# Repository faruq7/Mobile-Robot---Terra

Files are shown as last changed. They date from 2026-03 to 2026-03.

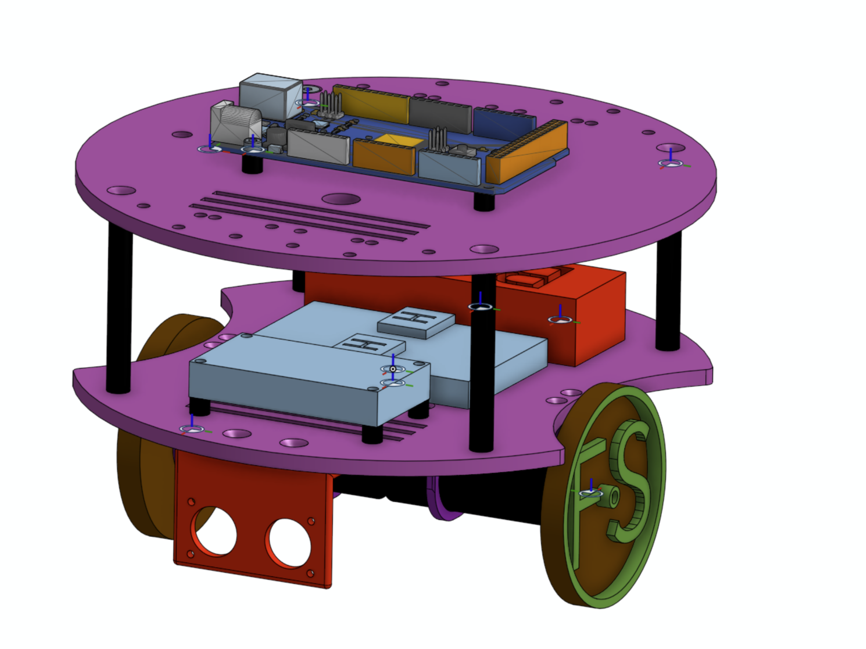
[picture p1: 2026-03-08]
CAD/Assembly/Assembly Image.png

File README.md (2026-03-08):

Objective:
To develop a mobile robot that is capable of reliable motion control, obstacle detection, and basic autonomous manoeuvres.

Mechanical & System Design:
•	Designed and modelled full chassis assembly in CAD using Onshape, including the motors, mounts, and incorporating techniques like clearance and interference checks to ensure ease of production and efficient assembly. 
•	Mechanical components were 3D printed and the electronics researched and then sourced.
•	Integrated dual DC motors with encoders for feedback-based motion control.
•	Utilised ultrasonic sensors for obstacle detection.
•	Developed program using the Arduino IDE.

Motion Control & Behaviour:
The robot was programmed using state machine logic to manage driving states which included:
•	Forward
•	Reverse
•	Left / Right turns
•	Three-point turn manoeuvre

Main Problem Encountered:
The robot had a slight drift to the left when doing standard forward motion. This highlighted there was unequal motor revolutions despite the motors possessing the same gear difference and drive commands.
Solution
The Encoder difference was then logged to an SD card during the forward motion. The data highlighted a substantial difference with the motor revolutions, confirming the imbalance of velocity between motors.
Proportional (P) control was then implemented with the aim of reducing the velocity difference between motors based on the encoder feedback.

Outcome
The forward motion drift had reduced slightly, although small cumulative error remains as on P control was implemented. Integral control will be added to compensate for the accumulated drift over longer distances.
Project Overview
System Architecture
Hardware
Software
How to Run
Images / CAD
Future Improvements

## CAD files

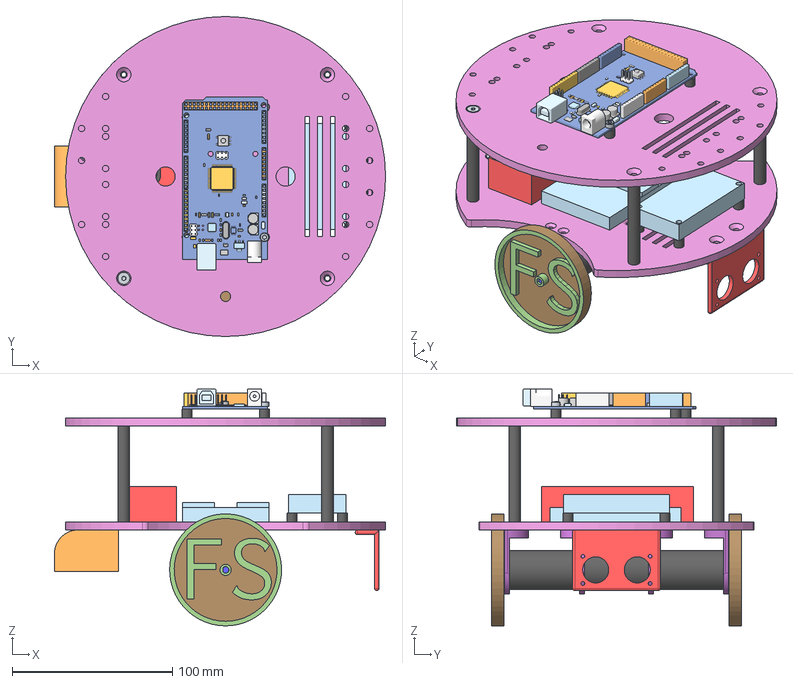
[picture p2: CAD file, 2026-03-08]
CAD/Assembly/Assembly 1.step
207.0 x 200.0 x 148.0 mm
Hex socket countersunk head screw M4x0.7 x 10 x 2
Hex socket countersunk head screw M4x0.7 x 40
Castor Spacer
Hex socket head cap screw M3x0.50 x 12
Hex socket countersunk head screw M4x0.7 x 35

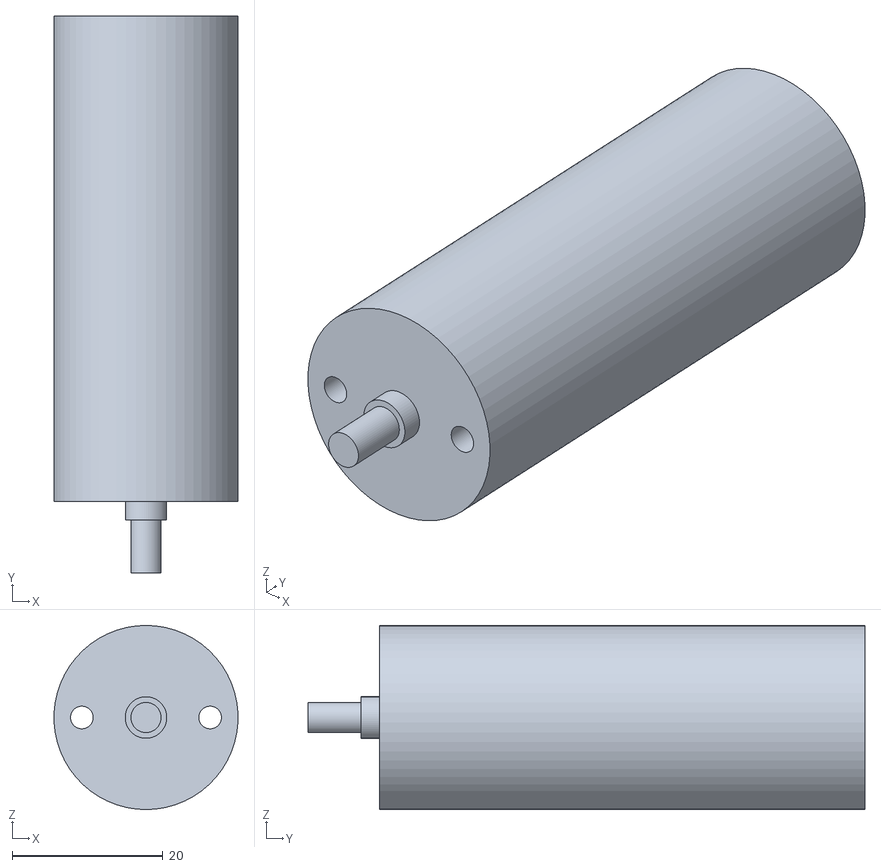
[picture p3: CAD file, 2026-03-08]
CAD/Parts/Motor - Part 1.stl
24.4 x 73.8 x 24.4

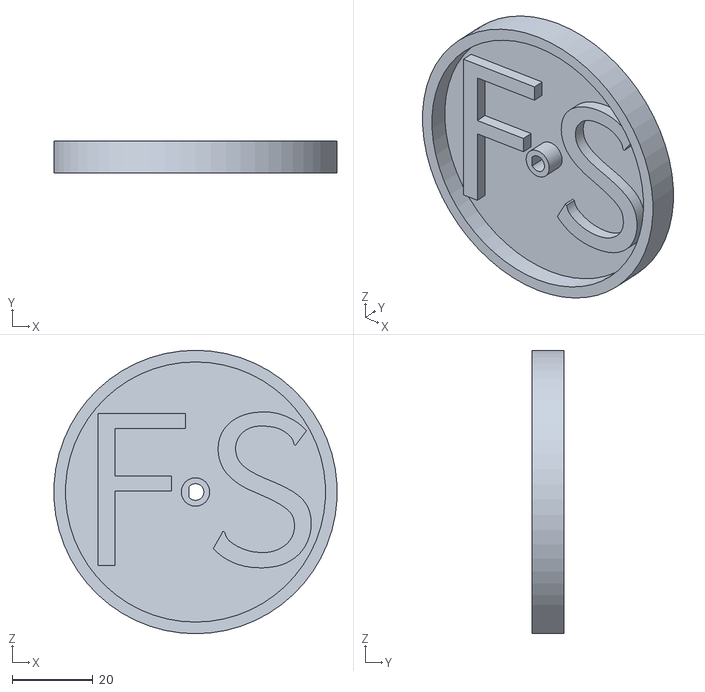
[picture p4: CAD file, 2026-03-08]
CAD/Parts/Wheels -.stl
69.9 x 8.00 x 70.0

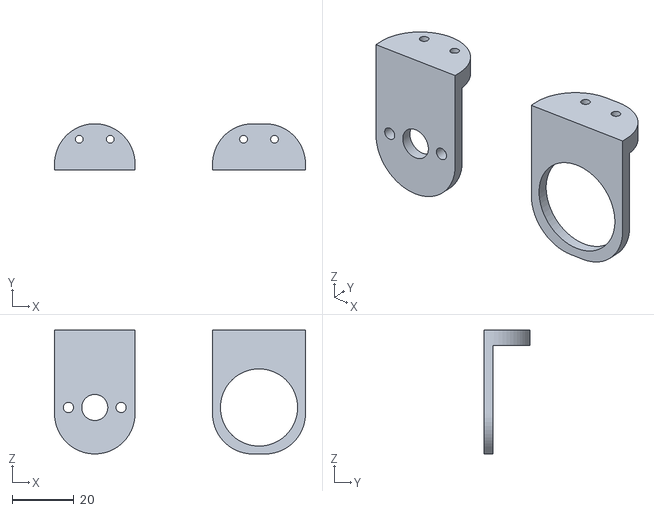
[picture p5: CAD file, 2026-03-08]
CAD/Parts/Motor Holder.stl
81.0 x 15.0 x 40.0

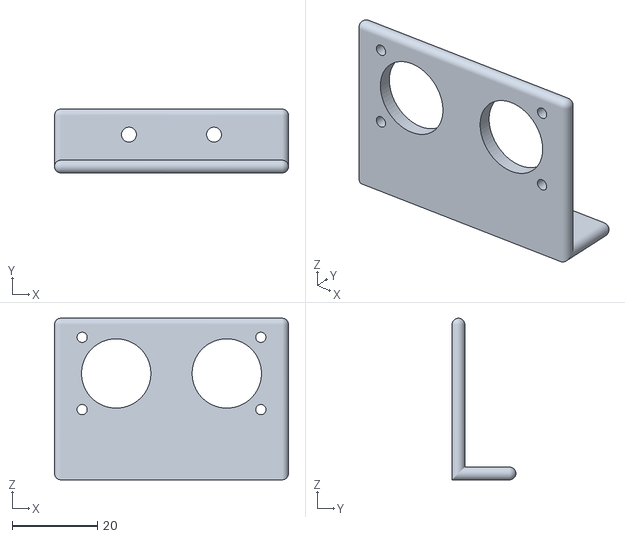
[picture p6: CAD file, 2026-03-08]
CAD/Parts/Ultrasonic sensor Holder.stl
55.0 x 15.0 x 38.0

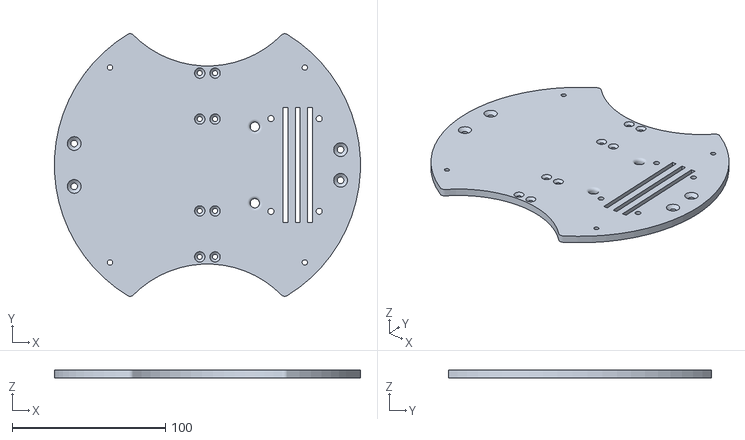
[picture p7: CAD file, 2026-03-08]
CAD/Parts/Base Layer.stl
199.9 x 171.6 x 5.00

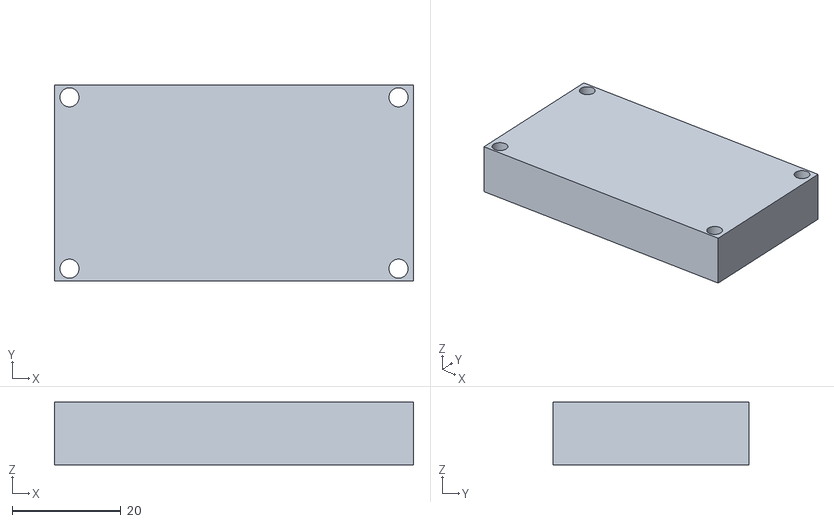
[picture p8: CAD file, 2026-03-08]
CAD/Parts/Buck Convertor - Part 1.stl
66.0 x 36.0 x 11.5

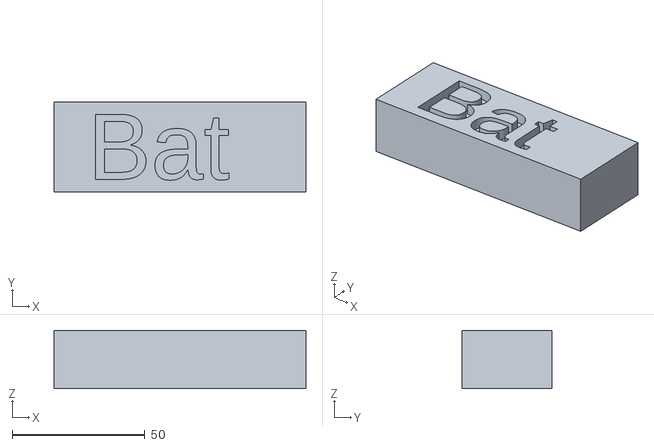
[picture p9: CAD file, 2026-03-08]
CAD/Parts/Battery - 3S - Part 1.stl
95.0 x 34.0 x 22.0

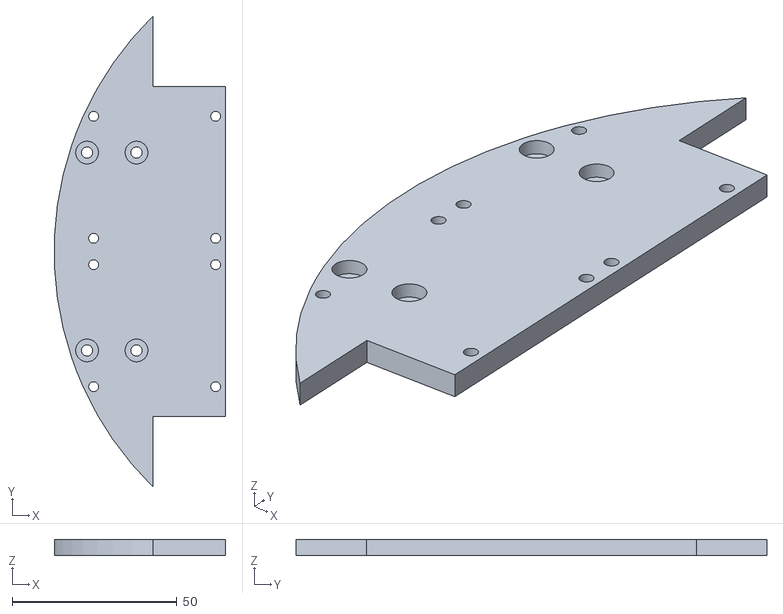
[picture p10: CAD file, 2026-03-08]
CAD/Parts/Motor Controller Adapter Plate.stl
51.9 x 142.8 x 5.00

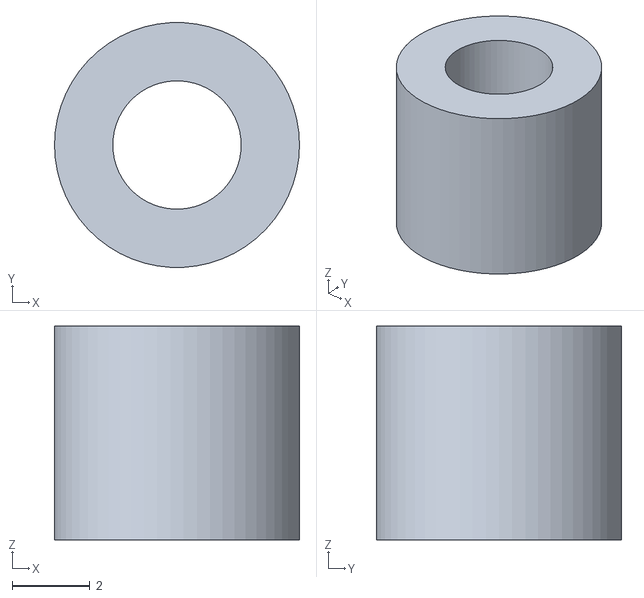
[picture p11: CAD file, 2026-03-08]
CAD/Parts/MCU Spacer - Part 1 (1).stl
6.30 x 6.29 x 5.50

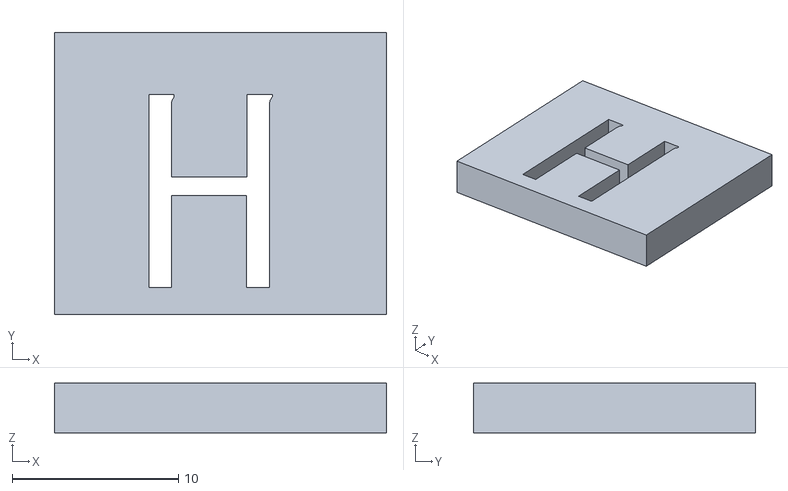
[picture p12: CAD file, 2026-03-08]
CAD/Parts/H bridge - Part 1.stl
20.0 x 17.0 x 3.00

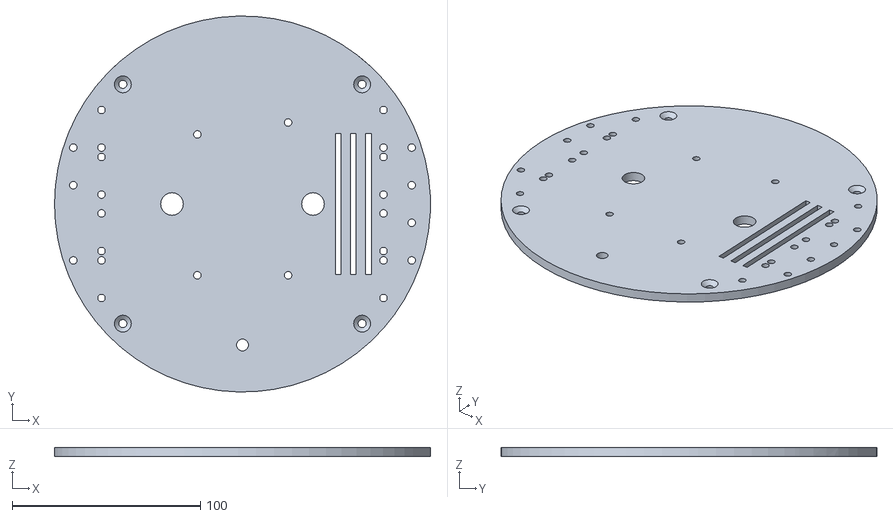
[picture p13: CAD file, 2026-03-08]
CAD/Parts/Second Layer.stl
200.0 x 199.9 x 5.00

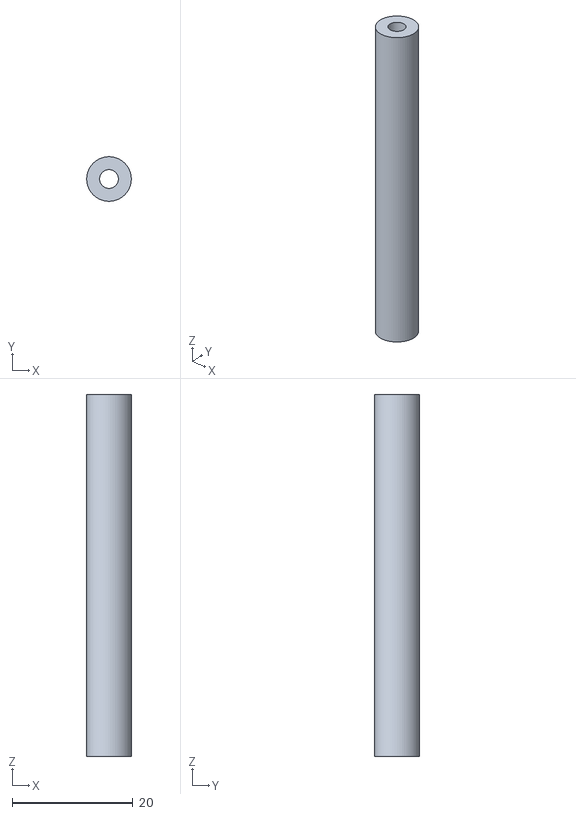
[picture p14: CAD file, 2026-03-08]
CAD/Parts/Base Spacer.stl
7.40 x 7.39 x 60.0

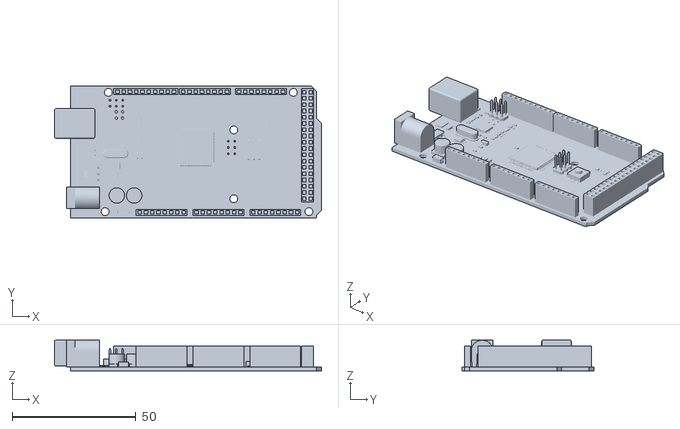
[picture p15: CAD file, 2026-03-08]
CAD/Parts/Arduino_Mega_2560_-_STL (2).stl
108.1 x 53.3 x 12.5

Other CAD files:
CAD/Parts/Breadboard - Part 1.stl
CAD/Parts/New H Bridge - Part 1.stl
CAD/Parts/Castor Spacer - Castor Spacer.stl

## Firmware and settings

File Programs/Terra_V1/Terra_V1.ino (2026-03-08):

//Call other libraries and scripts
//#include "Ultrasonic_Test.h"
//#include "Encoder.h"
//#include "Motor.h"
#include "Robot.h"

Robot Terra;


void setup(){
  Serial.begin(115200);  
  Terra.begin();
}




void loop(){
  //Plus_Ultra.get_distance();
  //Serial.print("LHS:  ");
  //Lhs_Encoder.debug();
  //Serial.print("RHS:  ");
  //Rhs_Encoder.debug();
  //Lhs_Encoder.Get_Pulses();
  //Rhs_Encoder.Get_Pulses();
  //Lhs_Encoder.Get_Revs();
  //Rhs_Encoder.Get_Revs();

 //Basic Motion()

  //Terra.Drive_Forward(100);
  //delay(812);
  
/*  Stop();
  Turn_Left();

  Drive_Backwards();
  Stop();
  Turn_Right();
  Stop();
  Point_Turn(Left);
  Stop();
  Point_Turn(Right);
  Stop();

*/
  //Ultrasonic Readings
  //Terra.get_distance();
  
  //Terra.Ultrasonic_Movement();
  //Terra.Set_Speed(120);
  //Terra.Encoded_Correction();


  //Encoded Motion
  //Terra.Encoded_Movement();
  //Terra.Stop();
  
  //Terra.Reset_Encoder();
  Terra.Move_cm(30);


  //delay(200);
}

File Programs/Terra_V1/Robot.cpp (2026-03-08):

#include "WString.h"
#include "HardwareSerial.h"
#include "Arduino.h"
#include "Robot.h"
#include "Ultrasonic_Test.h"
#include "Encoder.h"


// Left Motor
const int AIN_1 = 22;
const int AIN_2 = 23;
const int PWMA = 2;

//Right Motor
const int BIN_1 = 24;
const int BIN_2 = 25;
const int PWMB = 3;


Ultrasonic_Test Plus_Ultra;
Encoder Lhs_Encoder(20,21);
Encoder Rhs_Encoder(18,19);
Motor Lhs_Motor(AIN_1,AIN_2,PWMA, Left);
Motor Rhs_Motor(BIN_1,BIN_2,PWMB, Right);


bool flag_1 = false;
int val = 100;
float distance;

static long prevL = 0;
static long prevR = 0;

float distance_per_pulse = 0.0453;

Robot::Robot(){

}

void Robot::begin(){
  Lhs_Encoder.begin();
  Rhs_Encoder.begin();
  //Serial.println("started");

}

// Stop Robot dead in tracks
void Robot::Stop(){
  Lhs_Motor.Stop();
  Rhs_Motor.Stop();
  flag_1 = false;
  delay(1000);
}

// Robot Drive forward
void Robot::Drive_Forward(){
    Lhs_Motor.Straight_cm(speed);
    Rhs_Motor.Straight_cm(speed);
}


void Robot::Drive_Backwards(){
  Lhs_Motor.Backwards(100);
  Rhs_Motor.Backwards(100);
}






void Robot::Turn_Left(){
  Lhs_Motor.Turn_Left();
  Rhs_Motor.Turn_Left();
}


void Robot::Turn_Right(){
  Lhs_Motor.Turn_Right();
  Rhs_Motor.Turn_Right();
}

void Robot::Point_Turn(Side s){
  Lhs_Motor.Single_Point_Turn(s);
  Rhs_Motor.Single_Point_Turn(s);
  delay(1150);
}


void Robot::Deaccelerate(){
  Encoded_Movement();

  if (distance < 7.5 || distance > 1000) {
    Drive_Backwards();
  }

  if (distance >= 10 && distance <= 20){
    Lhs_Motor.Slow_Down(50);
    Rhs_Motor.Slow_Down(50);
  }
  else if(distance > 20 && distance <= 30){
    Lhs_Motor.Slow_Down(80);
    Rhs_Motor.Slow_Down(80);
  }
  else if(distance > 40 && distance <= 50){
    Lhs_Motor.Slow_Down(120);
    Rhs_Motor.Slow_Down(120);
  }
  else if(distance > 50 && distance <= 60){
    Lhs_Motor.Slow_Down(160);
    Rhs_Motor.Slow_Down(160);
  }
  else if(distance > 60 && distance <= 100){
    Lhs_Motor.Slow_Down(200);
    Rhs_Motor.Slow_Down(200);
  }
  else if(distance >= 7.5 && distance < 10){
    Stop();
  }

  Encoded_Movement();
}


void Robot::Encoded_Movement(){
  Lhs_Encoder.getCount();
  Rhs_Encoder.getCount();
  //Lhs_Encoder.debug();
  //Rhs_Encoder.debug();

}

float Robot::get_distance(){
  distance = Plus_Ultra.get_distance();
}


void Robot::Ultrasonic_Movement(){
  get_distance();
  Encoded_Correction();

  while (distance > 100 && distance < 1000){
    Drive_Forward(); 
    get_distance();
    Encoded_Correction();

  }

  Deaccelerate();
}



void Robot::Encoded_Correction(){
  long currL = Lhs_Encoder.Get_Pulses();
  long currR = Rhs_Encoder.Get_Pulses();

  long dL = currL - prevL;
  long dR = currR - prevR;

  prevL = currL;
  prevR = currR;

  Encoded_Movement();
  error = dL - dR;
  correction = constrain(Kp * error,-100,100);

  Serial.println("Display:" + String(error));

  if (error > 0){
    Lhs_Motor.Straight_cm(constrain(speed - correction,0,255));
    Rhs_Motor.Straight_cm(constrain(speed + correction,0,255));
    Serial.println("new RHS speed:" + String(speed + correction));
  }

    if (error < 0){
    Lhs_Motor.Straight_cm(constrain(speed + correction,0,255));
    Rhs_Motor.Straight_cm(constrain(speed - correction,0,255));
    Serial.println("new LHS speed:" + String(speed + correction));
  }

}

void Robot::Reset_Encoder(){
  if (Lhs_Motor.get_pins() == 0  && Rhs_Motor.get_pins() == 0){
    Lhs_Encoder.Reset_Counter();
    Rhs_Encoder.Reset_Counter();
  }
}


void Robot::Set_Speed(int _speed){
  speed = _speed;
}


void Robot::Move_cm(float distance){

  float current_pulse_L = Lhs_Encoder.Get_Pulses();
  float current_pulse_R = Rhs_Encoder.Get_Pulses();

  float pulses_required = distance/distance_per_pulse;

  while(Lhs_Encoder.Get_Pulses() < current_pulse_L + pulses_required){
    Drive_Forward();
  }
  Stop();
  delay(5000);

}













//V2
void Robot::Update_Motion(){

  switch (currentState) {

    case STOP:
      Stop();
      break;

    case FORWARD:
      Drive_Forward();
      break;

    case BACKWARD:
      Turn_Right();
      break;

    case TURN_LEFT:
      Turn_Left();
      break;

    case TURN_RIGHT:
      Turn_Right();
      break;
  }
}

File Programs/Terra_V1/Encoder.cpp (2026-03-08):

#include "WString.h"
#include "HardwareSerial.h"
#include "Arduino.h"
#include "Encoder.h"

//volatile long Encoder::EncoderCount_A1 = 0;
Encoder* Encoder::instance0 = nullptr;
Encoder* Encoder::instance1 = nullptr;

// Define Constructor
Encoder::Encoder(int a, int b){
  channel_a = a;
  channel_b = b;

}

//Define Functions

//Starts the interrupt function
void Encoder::begin(){
  Serial.println("Encoder : " + String(channel_a) + String(channel_b));
  pinMode(channel_a, INPUT_PULLUP);
  pinMode(channel_b, INPUT_PULLUP);
  
  if (!instance0) {
    instance0 = this;
    attachInterrupt(digitalPinToInterrupt(channel_a), isr0, RISING);
  }
  else if (!instance1) {
    instance1 = this;
    attachInterrupt(digitalPinToInterrupt(channel_a), isr1, RISING);
  }
  
}

void Encoder::isr0() {
    if (instance0) instance0->handleISR();
}

void Encoder::isr1() {
    if (instance1) instance1->handleISR();
}


//Calls the Interrupt to increment Encoder
void Encoder::handleISR(){
  if( digitalRead(channel_a) ){ 
    EncoderCount_A1++;
  }
  else{
    EncoderCount_A1--;
  }
}



long Encoder::Get_Pulses() {
  return EncoderCount_A1;
}

long Encoder::Get_Revs() {
  return EncoderCount_A1 / PPR;
}


void Encoder::getCount() {
    noInterrupts();
    long val = EncoderCount_A1;
    interrupts();
    Serial.println("Encoder" + String(channel_a) +" : " + String(val));
}

void Encoder::Reset_Counter(){
  noInterrupts();
  EncoderCount_A1 = 0;
  Serial.println("Resetting");
  interrupts();
}


void Encoder::debug(){
  Serial.print(String(channel_a) +" Pulses: ");
  Serial.print(Get_Pulses());
  Serial.print(" Revs: ");
  Serial.println(Get_Revs());
}
